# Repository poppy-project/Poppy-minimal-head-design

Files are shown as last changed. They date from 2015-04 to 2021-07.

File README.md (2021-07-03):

# Poppy minimal head design for Raspberry Pi 3
This is the Raspberry Pi 3 version for Poppy Torso and Poppy Humanoid. [Download STL files in the release section](https://github.com/poppy-project/Poppy-minimal-head-design/releases/tag/v2.0).

Poppy head for Raspberry Pi 3

This head was compatible with Manga screen v1 but this screen is no longer manufactured. If you need a screen please refer to the Raspberry Pi 4 version aka [**Poppy Eve** head design](https://github.com/poppy-project/Poppy-eve-head-design).

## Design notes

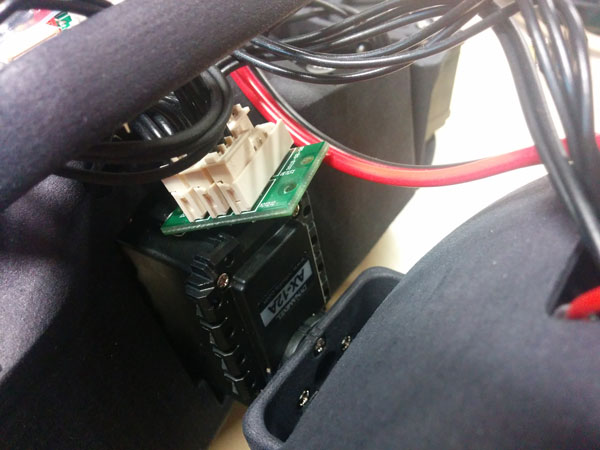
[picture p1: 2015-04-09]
doc/img/neck_connection.jpg

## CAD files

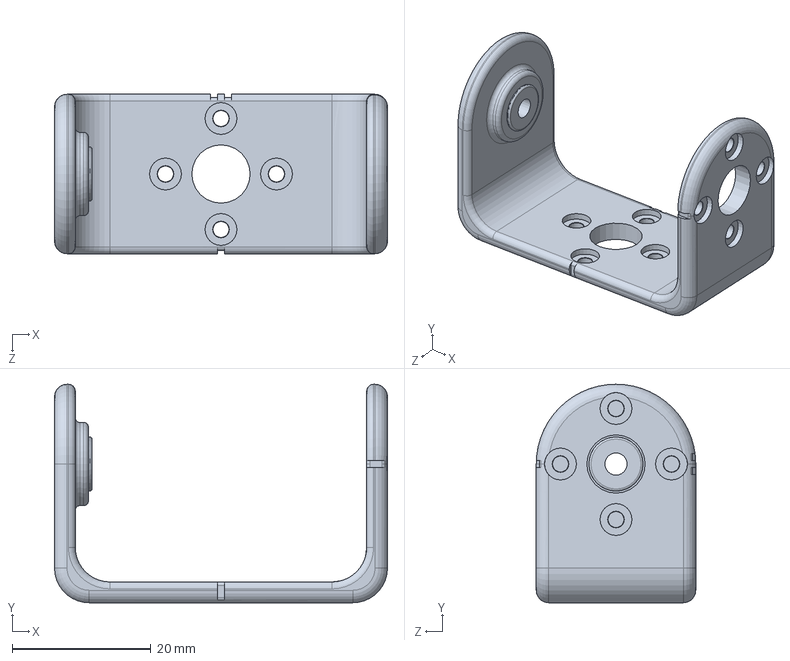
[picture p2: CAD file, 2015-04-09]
parts/neck.SLDPRT
48.0 x 31.5 x 23.0 mm

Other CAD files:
head.SLDASM
parts/screen_support.sldprt
parts/speaker_right.sldprt
parts/speaker_left.sldprt
parts/head_face.sldprt
parts/head_back.sldprt
parts/screen.sldprt
parts/camera_support.sldprt
parts/head_design.SLDPRT

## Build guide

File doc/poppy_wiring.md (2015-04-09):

# Poppy-humanoid wiring tutorial

This tutorial explain step by step how to wire your poppy-humanoid head.

##Motor network
1) Take the two longest 3P robotis wire and plug it to your two USB2AX.  
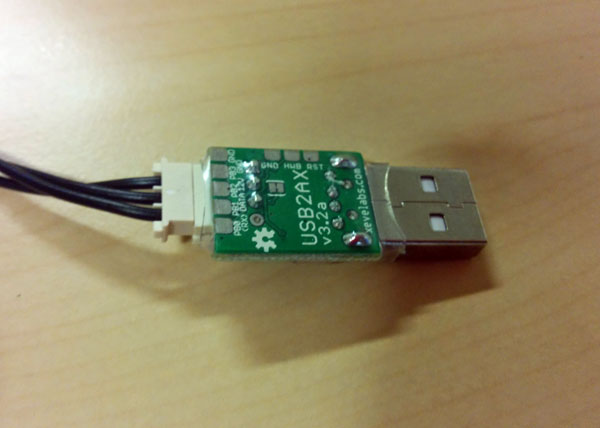
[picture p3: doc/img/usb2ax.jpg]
  
2) Pass the other side into the hole back to the Poppy's head.  
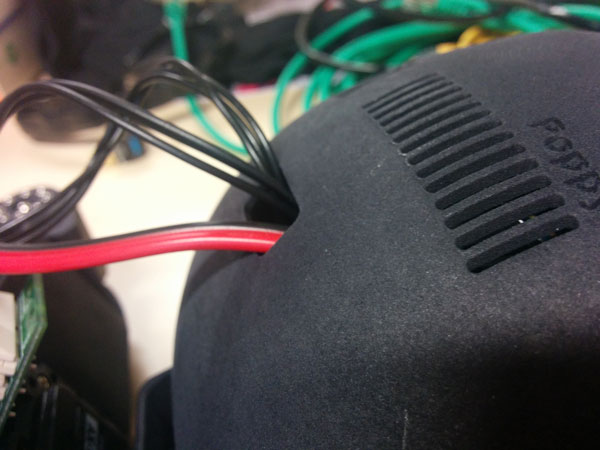
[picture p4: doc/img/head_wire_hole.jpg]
  
3) Plug one in the robotis dispatcher into the neck.  
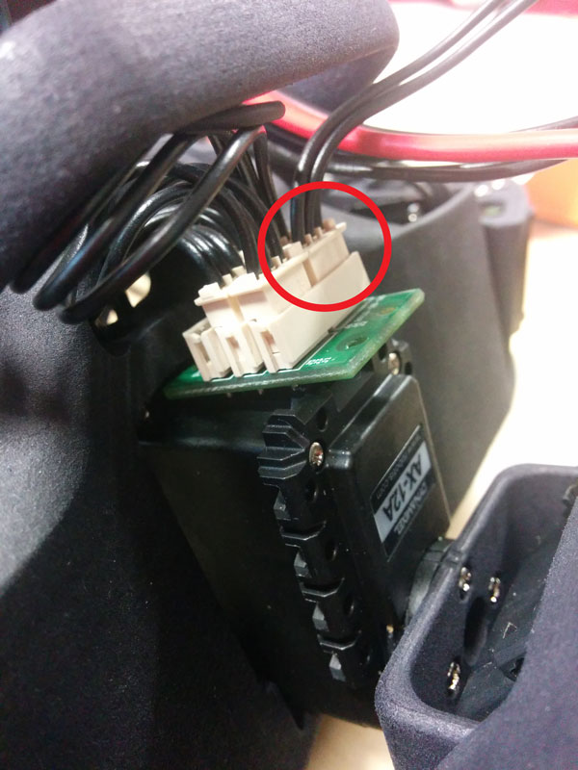
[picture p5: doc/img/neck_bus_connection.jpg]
  
4) Plug the other into the power board into the pelvis.  
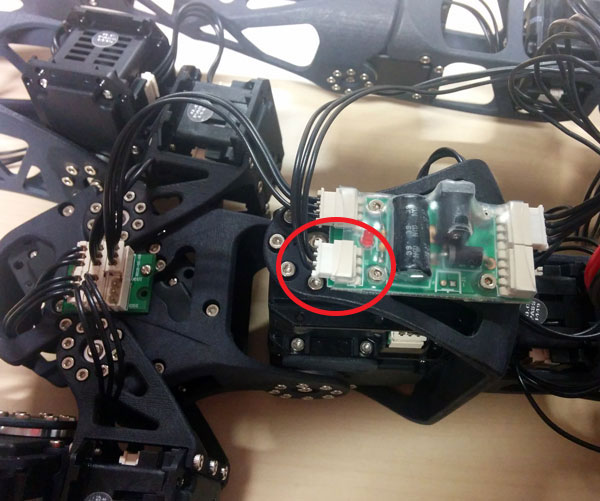
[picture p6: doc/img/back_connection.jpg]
  

##Power and sound of the head
1) Take your custom UBEC and pass the black/red wire with the 4P robotis connector into the hole back to the Poppy's head.  
  
2) Plug the 4p robotis connector in one of the robotis power board.  
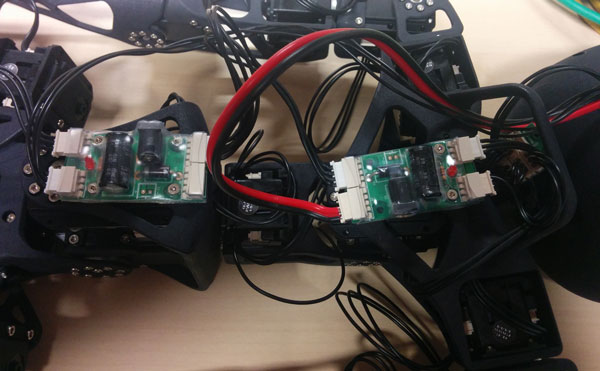
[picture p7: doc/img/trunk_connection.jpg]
  
3) Put the other side of the UBEC and the odroid power jack on the 2P green screw terminal of your audio amplificator (red on VDD and black into GND).  
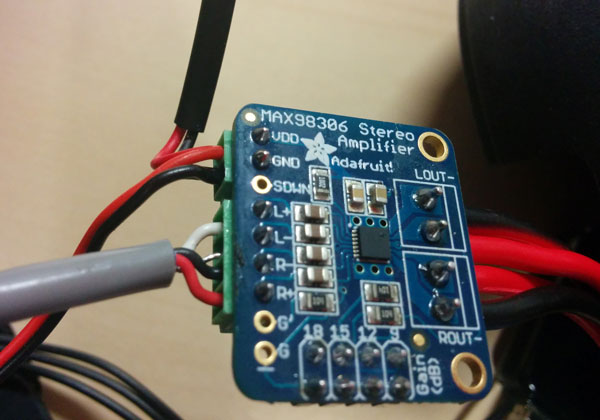
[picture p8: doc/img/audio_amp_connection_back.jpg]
  
4) Put the odroid audio jack on the 4p green screw terminal of your audio amplifier like this :  
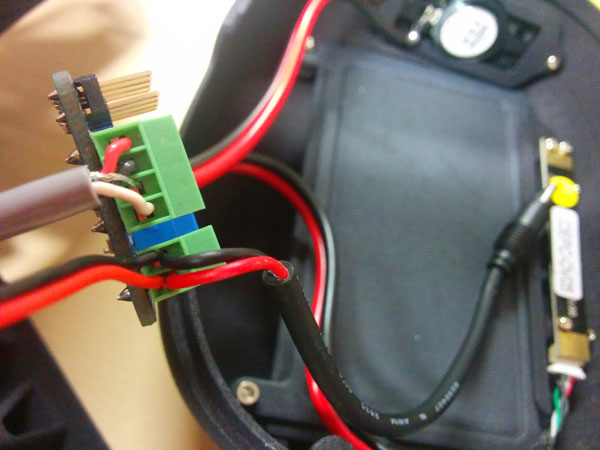
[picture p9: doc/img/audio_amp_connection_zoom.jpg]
  
5) Add your speaker into blue screw terminal of your amplifier.  
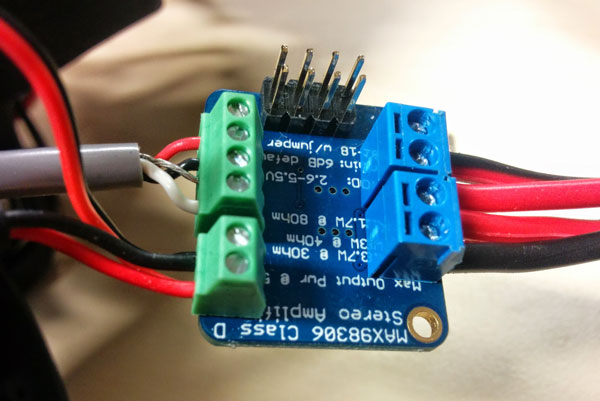
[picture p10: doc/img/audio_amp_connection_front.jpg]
  

##Final step
1) Connect the audio jack on your odroid.  
2) Mount your EMMC or SD memory card into your odroid.  
3) Set your odroid into the head.  
4) Plug your camera.  
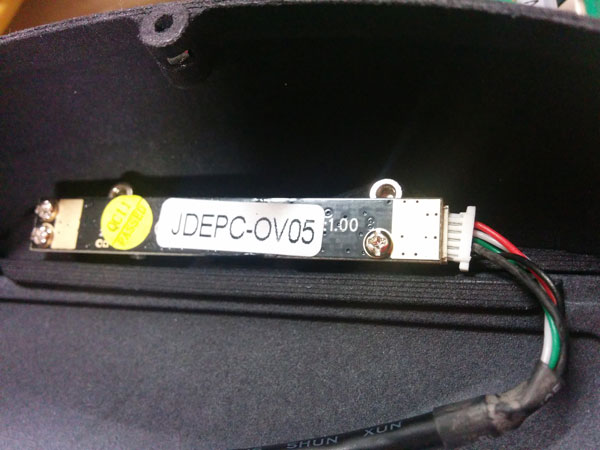
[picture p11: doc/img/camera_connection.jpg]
  
4) Connect the power jack on your odroid.  
5) Connect a usb hub on your odroid.  
6) Plug all your usb devices (camera, 2xUSB2AX, wifi).  
7) Close the head.  

##Poppy software environement installation
Please folow the [Poppy software installation readme](https://github.com/poppy-project/poppy_install)

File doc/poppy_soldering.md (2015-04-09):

# Poppy-humanoid soldering tutorial

This tutorial explain step by step how to produce custom wire needed to your poppy-humanoid.

You will need:

- [Audio Jack connector](http://fr.farnell.com/webapp/wcs/stores/servlet/ProductDisplay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)
- [Screw terminal connector 2P](http://fr.farnell.com/webapp/wcs/stores/servlet/ProductDisplay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)
- [Screw terminal connector 4P](http://fr.farnell.com/webapp/wcs/stores/servlet/ProductDisplay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)
- [Audio cable](http://fr.farnell.com/webapp/wcs/stores/servlet/ProductDisplay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)
- [Large heat shrink](http://fr.farnell.com/webapp/wcs/stores/servlet/ProductDisplay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)
- [Small heat shrink](http://fr.farnell.com/nte-electronics/47-23048-bk/heat-shrink-tubing-3mm-id-po-black/dp/2192424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)
- [Molex connector 4P](http://fr.farnell.com/webapp/wcs/stores/servlet/ProductDisplay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)
- [Contact Crimping](http://fr.farnell.com/webapp/wcs/stores/servlet/ProductDisplay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)
- [Black/red Cable](http://fr.farnell.com/pro-power/cb0043-red-black-100m/cable-2cond-0-44mm2-red-noir-par/dp/2425483)
- [Ubec](http://www.adafruit.com/product/1385)
- [Audio amplifier](http://www.adafruit.com/products/987)
- [Two speakers](http://fr.farnell.com/visaton/2941/loudspeaker-mini-oval-8-ohm/dp/1675524?ost=1675524)
- Electronique tools set

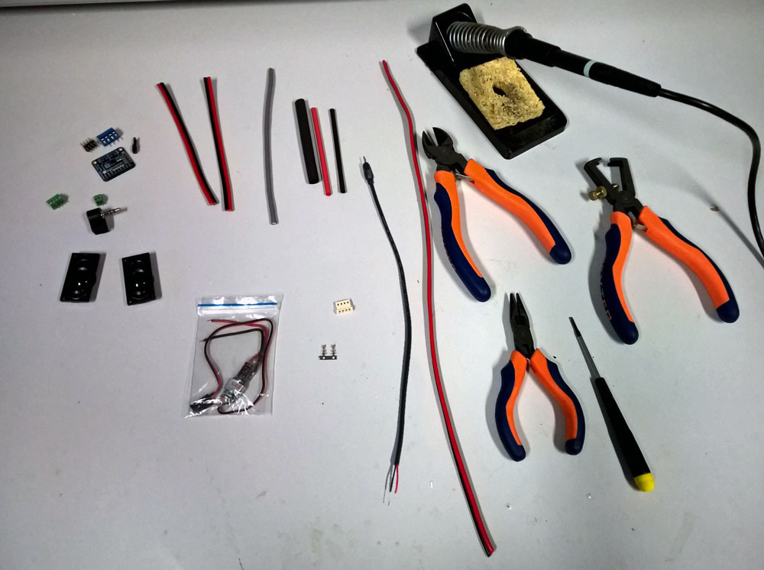
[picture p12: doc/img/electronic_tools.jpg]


## Power Supply
You will need:
- 30cm of **black/red cable**
- two **contact crimping**
- a **molex connector 4P**
- **Ubec**
- **Small heat shrink**
- **Large heat shrink**

1) Strip and foliate the 2 sides of your **Black/red cable**  
2) Crimp your **contact crimping**  
3) Put a small tin layer in your **contact crimping**
4) Place it in your **molex connector 4P**  
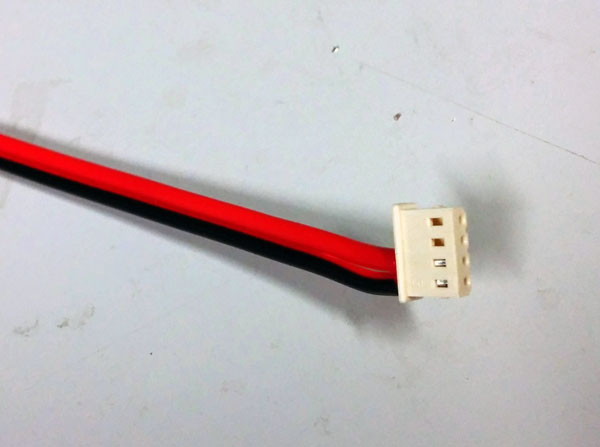
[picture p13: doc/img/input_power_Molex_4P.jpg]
  
5) Soldering the other side to the black and red cables of your **UBEC**. Do not forget to use 2 parts of **Small heat shrink** for each wire (black and red) and a **Large heat shrink** above.  
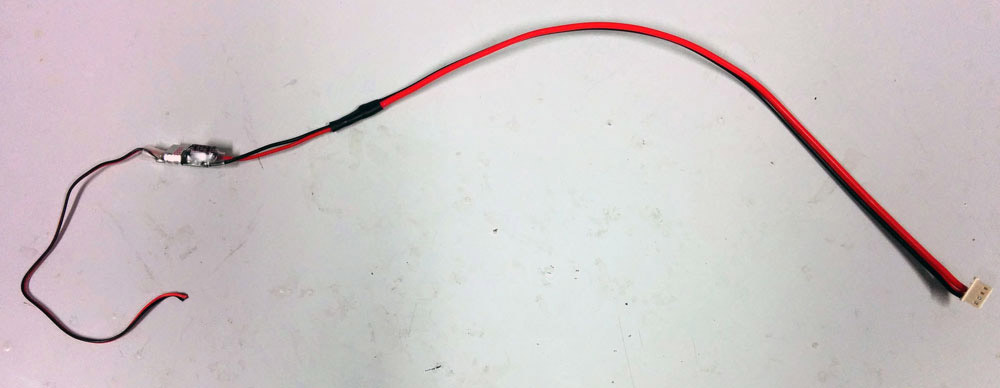
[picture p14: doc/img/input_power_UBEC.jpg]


## Sound

### Build a cable with stereo jack
You will need:
- 10cm of **Audio cable**
- **Audio Jack connector**
- **Large heat shrink**

1) Strip and foliate the 2 sides of your **Audio cable**
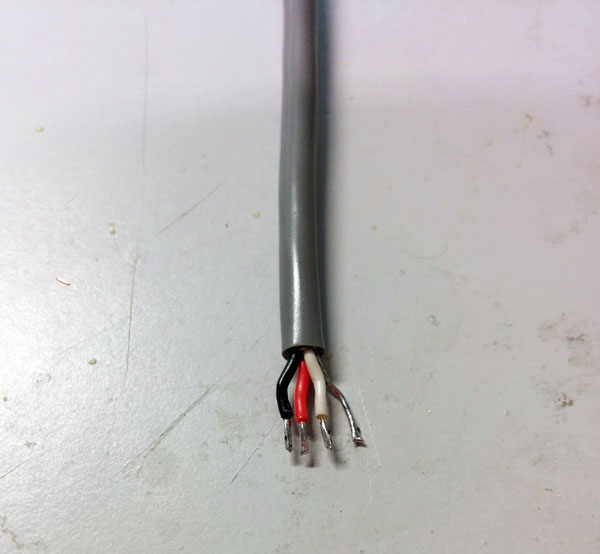
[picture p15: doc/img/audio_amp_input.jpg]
  
2) Soldering the **Audio Jack connector**  
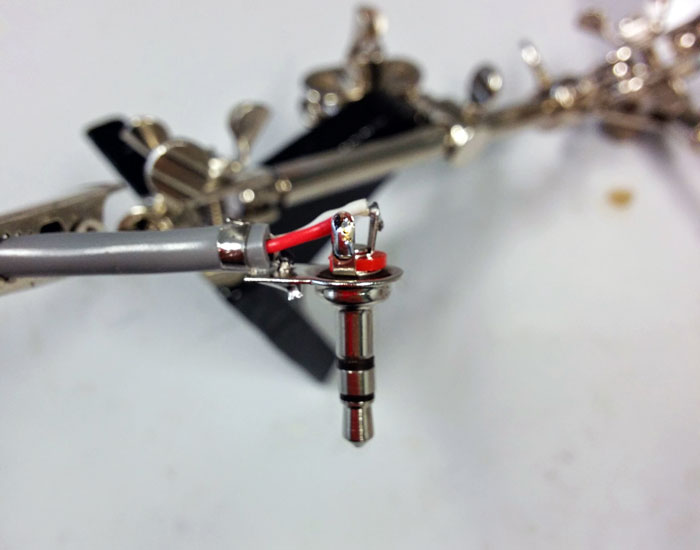
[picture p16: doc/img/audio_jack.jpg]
  
3) Do not use the **Audio Jack connector** cover (it will be too big for Poppy). Bend left and right contact of **Audio Jack connector** and cover it with **Large heat shrink**.
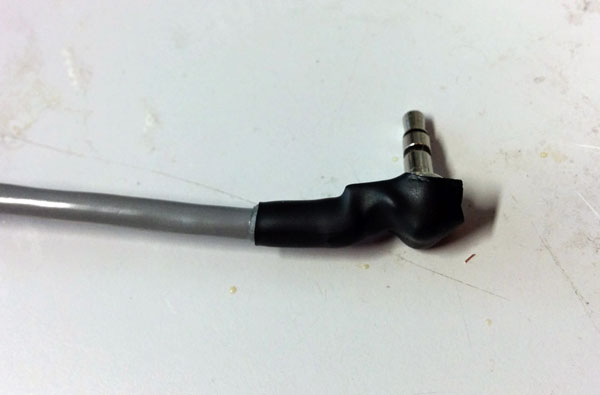
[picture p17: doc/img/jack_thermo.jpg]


### Solder components on the Adafruit stereo amplifier
You will need:
- **Screw terminal connector 2P**
- **Screw terminal connector 4P**
- **Audio amplifier**

1) Cut the two plasic pin of the **Screw terminal connector 2P**
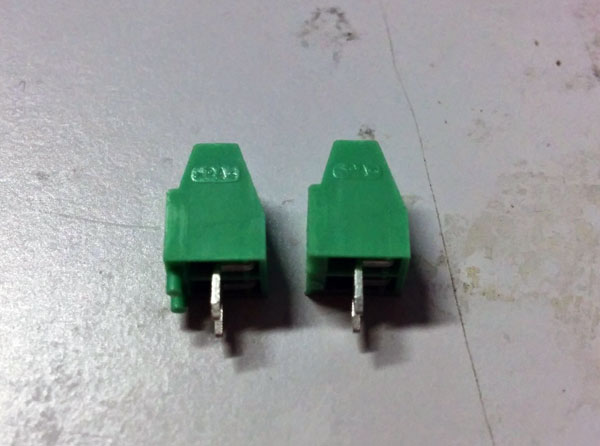
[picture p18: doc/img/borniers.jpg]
  
2) Soldering Blue screw terminal and 2x4p header given with the **Audio amplifier** kit.  
3) Soldering **Screw terminal connector 2P** on *VDD* and *GND* pins.  
4) Soldering **Screw terminal connector 4P** on *L+*, *L-*, *R+*, and *R-* pins.  

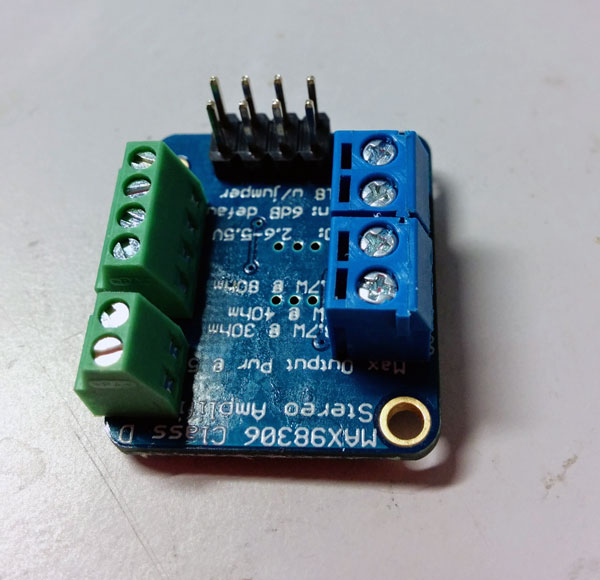
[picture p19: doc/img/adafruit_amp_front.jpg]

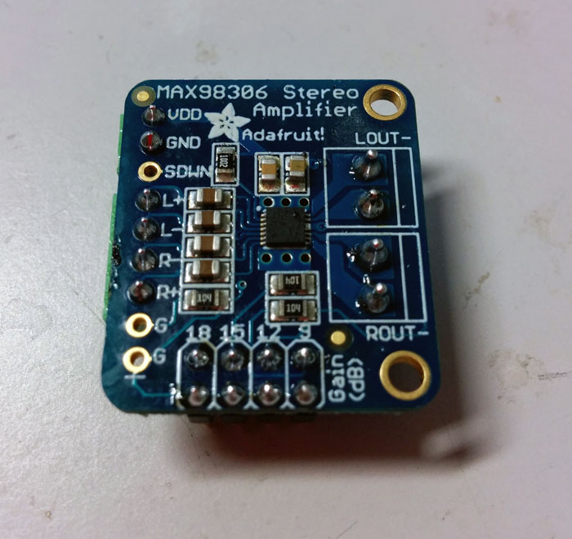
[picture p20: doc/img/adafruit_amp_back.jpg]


### Speakers
You will need:
- 2x15cm of **Black/red cable**
- **Two speakers**
- **Large heat shrink**

1) Strip and foliate the **2 SIDES** *(i.e. not like in the following picture)* of your **black/red cable** 
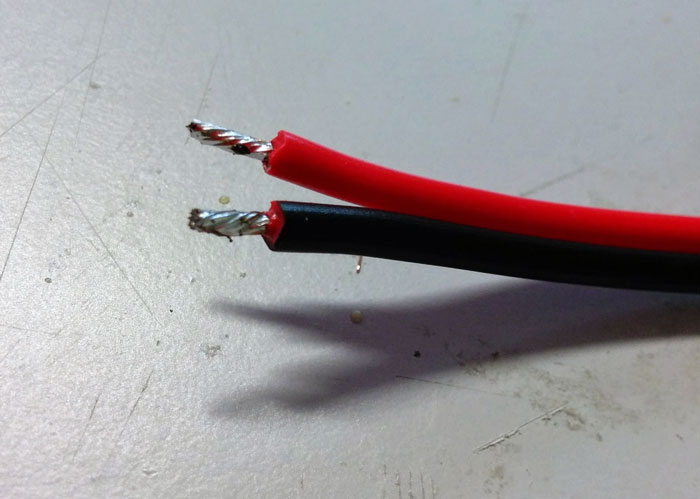
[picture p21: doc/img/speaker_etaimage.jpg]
  
2) Soldering it on your **Two speakers**  
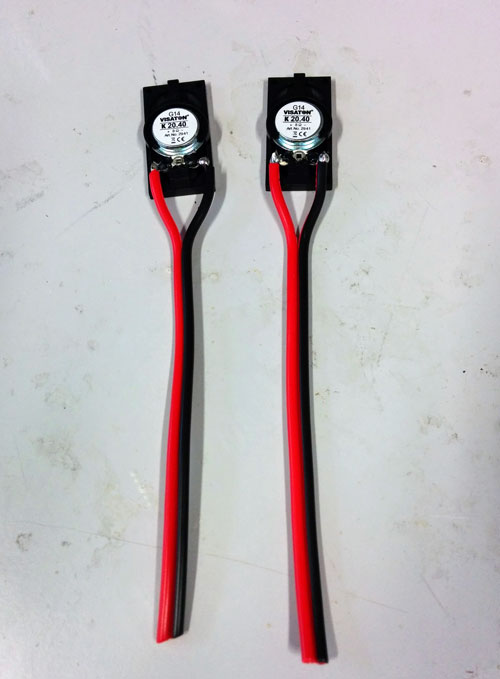
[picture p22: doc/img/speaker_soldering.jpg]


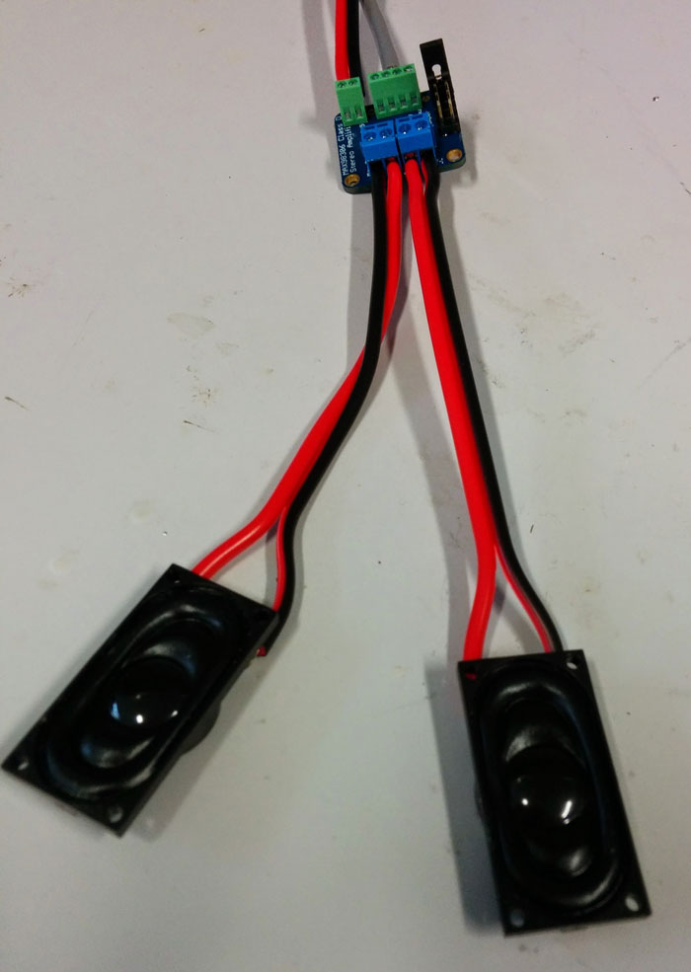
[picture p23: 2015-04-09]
doc/img/speaker_amp_assembly.jpg

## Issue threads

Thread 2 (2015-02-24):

Improve  Odroid U3 fixation robustness

matthieu-lapeyre, 2015-02-24:
- increase robustness of the front fixation arm
- add bolt/nut system on the rear fixation

Closed 2015-02-27.

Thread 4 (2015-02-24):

Speaker support screws M2x5mm seem too long ...

matthieu-lapeyre, 2015-02-24:

Closed 2015-02-27.

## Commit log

2015-01-13 add geometrical references for assembly (+2 squashed commit)
    Squashed commit:
    [ef383a5] add Poppy trademark on the head (+1 squashed commits)
    Squashed commits:
    [1ef1550] change dimensions to attach the screen
    [c8f79b2] add 3D printed parts of the Poppy Humanoid head
    [neck.SLDPRT]
2015-01-13 add off the shelf electronic components via submodules linked to Github Gist: - camera: Videw JDEPC - display: Manga screen - computer: Odroid U3 - speaker: Viston K20.40 - controller: USB2AX
2015-01-13 add Poppy Humanoid head assembly
2015-01-13 - add the fake manga screen - remove the neck part from the head assembly - update camera module hash
2015-02-27 -add multipurpose supports. Fix #8 - add support for the Adafruit MAX98306. Fix #7 - add speaker names. Fix #6 - fix the speaker support shape. Fix #3 - Fix #4 - Increase the robustness of the Odroid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
    MULTIKILL
    [camera_support.sldprt, neck.SLDPRT, screen.sldprt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]
2015-03-19 add a support for the Sparkfun Razor 9DoF IMU in the head.
2015-03-20 add the Sparkfun 9 DoF Razor IMU as submodule
2015-03-20 update imu module to include the Sparkfun razor model
2015-04-09 add all photos for the soldering instructions
2015-04-09 add tuto text for power supply assembly
2015-04-09 add photos for wiring instructions
2015-04-09 Motor connection
2015-04-09 power and sound connection
2015-04-09 include the Sparkfun IMU
2015-04-09 update polyamide material
    [camera_support.sldprt, neck.SLDPRT, screen.sldprt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]
2015-04-09 move camera support upright to avoid contact between the bolt head and the camera PCB Issue: https://forum.poppy-project.org/t/mechanical-interference-in-webcam-fixing-in-the-poppy-head/1201/
    [camera_support.sldprt]
2015-09-24 update design to fit with the XU4 panel connectors
2015-09-24 update extracted head-back part with the modification made for the XU4 board
2015-09-24 integration of the XU4 in the head assembly
2016-02-15 replace computer submodule with the raspberry model
2016-02-15 modify head back to integrate a raspberry pi 2
2016-02-15 integrate raspberry camera instead of the videw one update head parts
    [camera_support.sldprt, head_design.SLDPRT, screen.sldprt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]
2016-02-16 change camera hole to hide it more
    [head_design.SLDPRT]
2016-05-12 remove the support for the sparkfun IMU
    [head_design.SLDPRT]
2016-05-12 Reduce gap between transparent screen and head part
    [head_design.SLDPRT]
2016-05-12 add more support for the raspberry pi
    [head_design.SLDPRT]
2016-05-12 fix collision problem
    [head_design.SLDPRT]
2016-05-12 update head parts
    [camera_support.sldprt, head_back.sldprt, head_face.sldprt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]
2016-05-12 update assembly and suppress the sparkfun IMU
    [head.SLDASM]
2016-05-12 remove the imu submodule
